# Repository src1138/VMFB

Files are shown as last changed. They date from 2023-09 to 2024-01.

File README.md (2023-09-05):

A vending machine for birds that rewards them with food when they drop something in a hole. Electronics and enclosure materials cost <100 USD/EUR. I've designed a PCB and PVC pipe enclosure and dispenser (described below). The circuit is not complex, but I think a custom PCB makes it easier for people who are not electronics hobbyists to build this. I've made a few different enclosures ouot of scrap for this, but will share the PVC pipe enclosure details since it's sturdy, waterproof, and the materials can all be found at the hardware store.

There were two main inspirations for me to start and  document this project

- Hans Forsberg (https://www.youtube.com/channel/UCtkv3wuEP-Veur4iYJWkBgA) - designed his own machine and was the first person I learned of that had birds (magpies) bringing items to deposit on thier own
- Josh Klein (https://thecrowbox.com/) - makes his Crowbox designs freely available and supports people who want to build it

# MAIN FEATURES
- portable
- saves power until a warm body is present
- battery or mains powered
- one moving part
- accessible components and materials
- rodents can't break in and get the food
- cheap to build
- customizable

# ELECTRONICS, SENSORS, AND POWER

The circuit is all analog, using four NE555 timers and one LM358 dual op amp. The sensors are all made using IR phototransistors and IR LEDs. The PCB has headers broken out so you can monitor and control it with a microcontroller or SBC. It runs on 5-6VDC and uses ~10mA in standby (~20mA if timer and powerbank keep-alive are enabled), ~250mA when IR LEDs are on and ~400mA when the dispenser motor is running. A 10,000 mAh USB powerbank should last about a week.

- Powerbank Keep-Alive: 555 sinks current every 7-22 seconds for 0.7-2.2 seconds to keep USB power banks on while sensors are in standby - the powerbank keep-alive can be disabled.
- IR LED ON/OFF: 555 keeps the IR LEDs used by the sensors on for 22 seconds after the last PIR trigger
- Op Amps: LM358 used as comparators to adjust the threshold of the sensors and send signals when they are triggered
- Motor Controller: 555 turns on the dispenser vibration motor when the deposit sensors are triggered, tuns it off when the dispense sensor is triggered
- Timed Dispense: 555 dispenses food every 10-100min - timed dispense can be disabled
- Daytimer: Phototransistor that puts the timer in reset while it's dark outside - brightness threshold can be adjusted or disabled (Rev. B)
- PIR Sensor: Sends a signal to turn on the sensor IR LEDs
- Deposit/Dispense Sensors: IR phototransistors and IR LEDs used as proximity sensors to monitor the deposit and dispense chutes
- Hopper Level Sensor: IR phototransistor and IR LED to detect when the food level gets low (Rev. B)
- Monitoring/Control: lines for monitoring and triggering events with an external controller (Rev. B)

# PCB, BOM AND GERBERS

Kicad Files (Github): https://github.com/src1138/VMFB

Gerbers and PCB (PCBWay): https://www.pcbway.com/project/shareproject/Vending_Machine_for_Birds_eda585b3.html

Front


Back


The PCB has footprints for USB type A, USB type B, barrel jack and screw terminal power input. You only need to populate the ones you will use.

In Rev.B Ver.1.0 you need to add a 10K resistor on the EMPTY sensor from the SIGNAL header pin to ground.

The Timer and Powerbank Keep-Alive are not essential and you don't have to populate the parts for them if you don't need/want to use them.

# CRITICAL COMPONENTS

This project uses commodity components, and you can confidently use alternatives with similar specs. There are a few points to keep in mind.

- For the phototransistors, they should have a photocurrent of around 10mA. If they have a lower photocurrent, you should replace the 10K resistors on the non-invertine op amp imputs with a higher value. For  instance, if your phototransistors have a photocurrent of ~1mA, use a 100K resistor intead.
- I use NE555Ps here - you could use other models, but keep in mind that the transistors controlling the IR LEDs (BD139) and motor (TIP41C) need a bit of current to their base. If for instance you use the CMOS 555 that can only source about 10mA, you may need to replace these transistors with ones that have more gain.

# HOW IT WORKS

## States
- Standby - No PIR trigger in the last 22 secs (IR LEDs are off)
- Sensors On - PIR was triggered in the last 22 secs (IR LEDs are on)
- Dispensing - Dispenser motor is on

## Modes

- Normal (dispenses on deposit)
- Timer (dispenses every x minutes AND dispenses on deposit)

## Event Sequence

1. PIR sensor sees a warm body
2. PIR triggers IR LED 555
3. IR LED 555 turn on sensor IR LEDs for 22 secs after last PIR trigger
4. When something is dropped in the deposit hole, the deposit sensor sees it
5. The deposit side of the dual op amp sends a pulse to trigger the motor 555
6. The motor 555 turns on the vibration dispenser motor - it times out after 11 secs
7. When something is dispensed, the dispense sensor sees it 
8. The dispense side of the dual op amp sends a pulse to reset the motor 555
9. The dispenser motor is stopped

When timed dispense is triggered, it sends a signal to turn on the sensor IR LEDs and triggers the motor controller to start the vibration dispenser. When something is dispensed, the motor stops.

# FAILURE MODES
- Deposit sensor jammed: Sensor will not trigger a dispense event until it is unjammed. The sensor uses an inline capacitor to limit the signal to a pulse each time it is triggered.
- Dispense sensor jammed: Vending machine will not dispense until the sensor is unjammed.
- Peanut hopper jammed or empty: Dispense motor will stop after ~10 seconds.

# MONITORING

I was using a Rasperry Pi Zero W with a wide-angle camera module with my vending machine, but I wanted something that drew less power (and was cheaper and more available). I found that the ESP32-CAM module  consumes about 135 MA when streaming video, can be put to sleep (consuming just a few mA) and has 4 GPIO pins available when using the SD-card slot - it can stream/record video and log events from the vending machine, making it all available over wifi or bluetooth.

I'm still in the process of modifying the ESP32-CAM example program to monitor/log events and stream video, record video files to SD, and sleep until the PIR is triggered. I will put this code on Github when it's ready.

# DISPENSER, ENCLOSURE, AND MOUNTING

Dispenser: two-layer vibration platform with offset holes made from 3mm PVC sheet and 15mm M3 brass standoffs. I used a small 24x12mm 2VDC motor attached to the dispenser with brass standoffs and 3mm PVC sheet.


Enclosure: made from 110mm and 50mm PVC pipe and joints, 32mm PVC joints, a 35mm plastic tray and a 1.5l PET bottle. 


Mounting: can be mounted on the ground, horizontal or vertical railing, wooden fence, wall, pole 
The dispenser typically dispenses a peanut or two within 3 seconds. Since it is a vibration dispenser, the enclosure should be level and mounted securely to insure relaible dispensing. 

The dispenser drops peanuts into a funnel made from the top of the PET bottle. There is about 12cm between the two, making it difficult for rodents small enough to get into the machine to get to the food. PVC is tough enough to keep larger rodents from gnawing or breaking thier way in.

# FEED

I used peanuts in the shell to attract birds to the area and shelled peanuts in the vending machine. If you live in an area with lots of pigeons, using peanuts in the shell will not attract them as much since they can't eat them (can't get he shell off) and you have a better chance of attracting corvids. Shelled peanuts are easier to dispense reliably - peanuts in the shell are less dense, more irregular in shape, and jam easily. Dry cat and dog food also works.

# BIRD CONDITIONING

Along with learning and having some fun, the goal is to get a birds to bring something, drop it in a hole, and get a reward. Birds need some conditioning for this, so there are a few phases to progress though to help them figure this out.

## Conditioning Stages
0 - Put food in the area you plan to mount the vending machine to start attracting birds
(1-2 weeks)
1 - Food Provided, Timed Dispense, Deposit Provided
(2-3 weeks)
2 - No Food Provided, Timed Dispense, Deposit Provided
(3-4 months)
3 - No Food Provided, No Timed Dispense, Deposit Provided
(6-8 months)
4 - No Food Provided, No Timed Dispense, No Deposit Provided

Time estimates are based on my own experience over the past year or so, but Phase 3 duration is a guess. As of July 2023 I have not yet seen a bird deposit an item I didn't provide. Unfortunately I had to take my machine down in May due to some new HOA regulations prohibiting feeding the birds in my neighborhood. I plan to redeploy it when I find another suitable location.

# PVC ENCLOSURE 

The PVC enclosure contains the battery, electronics and sensors, dispenser, peanuts, and deposited items. The platform is a 35cm plastic tray for a plant pot, attached to the deposit chute with 4 90-degree brackets, four M4 bolts and two hose clamps.

I used bits of electrical or duct tape to make the PVC pipes and joints fit securely tight. This way it is easy to disassemble/modify/repair. It's a good idea to wrap upward-facing joints to prevent water ingress during heavy rains.

You can load peanuts (or whatever) by unscrewing the top cap and pouring them in. I made two baffles from 3mm PVC sheet to reduce the pressure on the vibration dispenser.

You can unload the deposited items by unscrewing one of the caps on the lower half of the vending machine.

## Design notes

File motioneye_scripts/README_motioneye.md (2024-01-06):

GPIO Pins Used
You can use whatever pins you want, but I chose the following as they all default as inputs at boot.
- Sensor IR Control (SIRCON)=25 
- Dispenser Control (DISCON)=11
- PIR Monitor=27
- Sensor IR Monitor=17
- Timer Monitor=22
- Feed Level Monitor=23
- Deposit Monitor=24 
- Dispense Monitor=10 

/boot/config.txt
Add the following to make your control outputs drive low
gpio=11,25=op,dl

All the scripts go in /data/etc/
- userinit.sh: turns off HDMI and starts logging and camera enable/disable scripts
- VMFB_logger.py: logs the deposit and dispense events
- VMFB_logger.sh: logs PIR, Sensor IR, Timer and Feed Level status and trigger counts
- camera_on-off_schedule: sets the time for the camera to be enabled and disabled to save power
- monitor_1: displays logging and monitoring information on the video overlay
- alarm_on_1 and alarm_off_1: show as action buttons on the web interface to manually start and stop recording
- down_1: show as action buttons on the web interface to manually dispense feed

Config files also go in /data/etc/
- camera-1.conf (camera-1.conf.enable_camera/camera-1.conf.disable_camera): configuration files are overwritten to enable/disable the camera before restarting the motioneye server
- motion.conf (motion.conf.enable_camera/motion.conf.disable_camera): configuration files are overwritten to enable/disable the camera before restarting the motioneye server

Logs will be generated in /data/log/
- VMFB_YYY-MM-DD.log: daily log of events
- userinit.log: logs output from scripts called from userinit.sh
- prev_valPIR, prev_valSIR, prev_valTMR, prev_valEMT: logs the state of the previous execution of the VMFB_logger.sh so only changes will be logged
- 

If you want to specify timed dispense in a script instead of using the 555-based timer, you can try out VMFB_timer.sh.

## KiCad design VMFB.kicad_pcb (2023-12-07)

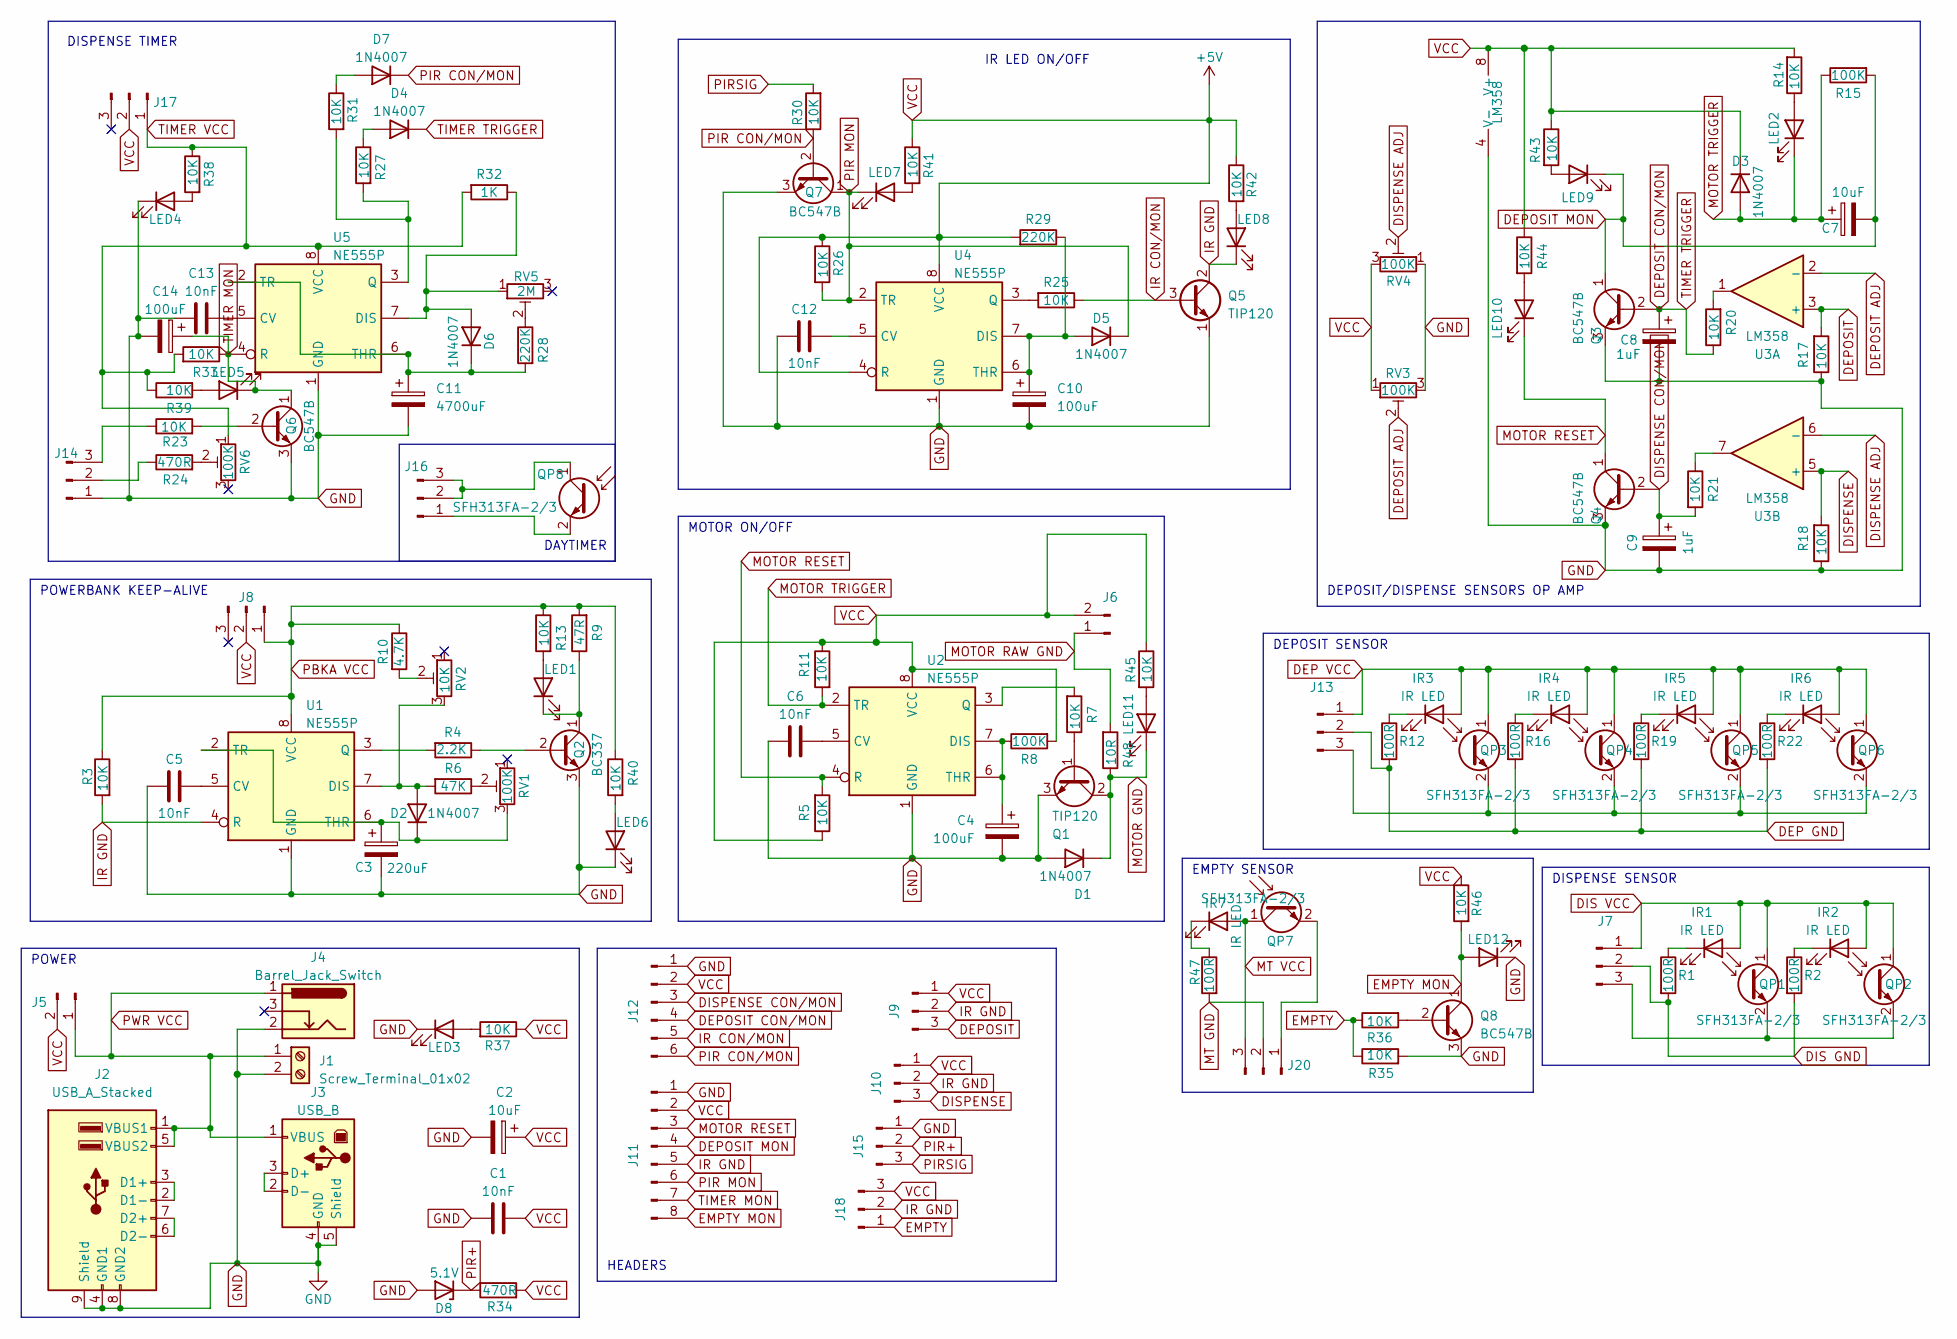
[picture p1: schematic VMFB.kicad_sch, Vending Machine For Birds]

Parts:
C1, C5, C6, C12, C13: 10nF; C_Disc_D5.0mm_W2.5mm_P5.00mm
C2, C7: 10uF; CP_Radial_D5.0mm_P2.00mm
C3: 220uF; CP_Radial_D8.0mm_P3.50mm
C4, C10, C14: 100uF; CP_Radial_D6.3mm_P2.50mm
C8, C9: 1uF; CP_Radial_D5.0mm_P2.00mm
C11: 4700uF; CP_Radial_D16.0mm_P7.50mm
D1, D2, D3, D4, D5, D6, D7: 1N4007; D_DO-41_SOD81_P2.54mm_Vertical_KathodeUp
D8: 5.1V; D_DO-41_SOD81_P2.54mm_Vertical_KathodeUp
IR1, IR2, IR3, IR4, IR5, IR6, IR7: IR LED; LED_D5.0mm
J1: Screw_Terminal_01x02; TerminalBlock_Altech_AK300-2_P5.00mm
J2: USB_A_Stacked; USB_A_Wuerth_61400826021_Horizontal_Stacked
J3: USB_B; USB_B_Lumberg_2411_02_Horizontal
J4: Barrel_Jack_Switch; BarrelJack_Horizontal
J5, J6: Conn_01x02_Pin; PinHeader_1x02_P2.54mm_Vertical
J7, J8, J9, J10, J13, J14, J15, J16, J17, J18, J20: Conn_01x03_Pin; PinHeader_1x03_P2.54mm_Vertical
J11: Conn_01x08_Pin; PinHeader_1x08_P2.54mm_Vertical
J12: Conn_01x06_Pin; PinHeader_1x06_P2.54mm_Vertical
LED1, LED2, LED3, LED4, LED5, LED6, LED7, LED8, LED9, LED10, LED11, LED12: Signal LED; LED_D5.0mm
Q1, Q5: TIP120; TO-220-3_Vertical
Q2: BC337; TO-92_Inline_Wide
Q3, Q4, Q6, Q7, Q8: BC547B; TO-92_Inline_Wide
QP1, QP2, QP3, QP4, QP5, QP6, QP7, QP8: SFH313FA-2/3; LED_D5.0mm
R1, R2, R12, R16, R19, R22, R47: 100R; R_Axial_DIN0207_L6.3mm_D2.5mm_P2.54mm_Vertical
R3, R5, R7, R11, R13, R14, R17, R18, R20, R21, R23, R25, R26, R27, R30, R31, R33, R35, R36, R37, R38, R39, R40, R41, R42, R43, R44, R45, R46: 10K; R_Axial_DIN0207_L6.3mm_D2.5mm_P2.54mm_Vertical
R4: 2.2K; R_Axial_DIN0207_L6.3mm_D2.5mm_P2.54mm_Vertical
R6: 47K; R_Axial_DIN0207_L6.3mm_D2.5mm_P2.54mm_Vertical
R8, R15: 100K; R_Axial_DIN0207_L6.3mm_D2.5mm_P2.54mm_Vertical
R9: 47R; R_Axial_DIN0309_L9.0mm_D3.2mm_P2.54mm_Vertical
R10: 4.7K; R_Axial_DIN0207_L6.3mm_D2.5mm_P2.54mm_Vertical
R24, R34: 470R; R_Axial_DIN0207_L6.3mm_D2.5mm_P2.54mm_Vertical
R28, R29: 220K; R_Axial_DIN0207_L6.3mm_D2.5mm_P2.54mm_Vertical
R32: 1K; R_Axial_DIN0207_L6.3mm_D2.5mm_P2.54mm_Vertical
R48: 10R; R_Axial_DIN0414_L11.9mm_D4.5mm_P5.08mm_Vertical
RV1, RV3, RV4, RV6: 100K; Potentiometer_Piher_PT-10-V10_Vertical
RV2: 10K; Potentiometer_Piher_PT-10-V10_Vertical
RV5: 2M; Potentiometer_Piher_PT-10-V10_Vertical
U1, U2, U4, U5: NE555P; DIP-8_W7.62mm
U3: LM358; DIP-8_W7.62mm

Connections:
DEP GND: J13.2, R12.2, R16.2, R19.2, R22.2
DEP VCC: IR3.2 (A), IR4.2 (A), IR5.2 (A), IR6.2 (A), J13.1, QP3.1 (C), QP4.1 (C), QP5.1 (C), QP6.1 (C)
DEPOSIT: J9.3, R17.2, U3.3 (+)
DEPOSIT ADJ: RV3.2, U3.2 (-)
DEPOSIT CON/MON: C8.1, D4.1 (K), J12.4, Q3.2 (B), R20.1
DEPOSIT MON: C7.2, J11.4, LED9.1 (K), Q3.1 (C), R15.2
DIS GND: J7.2, R1.2, R2.2
DIS VCC: IR1.2 (A), IR2.2 (A), J7.1, QP1.1 (C), QP2.1 (C)
DISPENSE: J10.3, R18.2, U3.5 (+)
DISPENSE ADJ: RV4.2, U3.6 (-)
DISPENSE CON/MON: C9.1, J12.3, Q4.2 (B), R21.2
EMPTY: J18.1, R35.1, R36.1
EMPTY MON: J11.8, LED12.2 (A), Q8.1 (C), R46.2
GND: C1.2, C2.2, C3.2, C4.2, C5.2, C6.2, C8.2, C9.2, C10.2, C11.2, C12.2, C13.2, C14.2, D1.2 (A), D8.2 (A), J1.2, J2.4 (GND1), J2.8 (GND2), J2.9 (Shield), J3.4 (GND), J3.5 (Shield), J4.2, J11.1, J12.1, J14.1, J15.1, LED3.1 (K), LED4.1 (K), LED6.1 (K), LED12.1 (K), Q1.3 (E), Q2.3 (E), Q3.3 (E), Q4.3 (E), Q5.1 (E), Q6.3 (E), Q7.3 (E), Q8.3 (E), R17.1, R18.1, R35.2, RV3.3, RV4.1, U1.1 (GND), U2.1 (GND), U3.4 (V-), U4.1 (GND), U5.1 (GND)
IR CON/MON: J12.5, Q5.3 (B), R25.1
IR GND: J9.2, J10.2, J11.5, J18.2, LED8.1 (K), Q5.2 (C), R3.2, U1.4 (R)
MOTOR GND: D1.1 (K), LED11.1 (K), Q1.2 (C), R48.1
MOTOR RAW GND: J6.1, R48.2
MOTOR RESET: J11.3, LED10.1 (K), Q4.1 (C), R5.2, U2.4 (R)
MOTOR TRIGGER: C7.1, D3.2 (A), LED2.1 (K), R11.2, R15.1, U2.2 (TR)
MT GND: J20.2, R47.2
MT VCC: IR7.2 (A), J20.3, QP7.1 (C)
unnamed: D2.2 (A), R6.2, RV2.3, U1.7 (DIS)
unnamed: C3.1, D2.1 (K), RV1.3, U1.2 (TR), U1.6 (THR)
unnamed: D4.2 (A), R27.1
unnamed: C10.1, D5.2 (A), R29.1, U4.6 (THR), U4.7 (DIS)
unnamed: D6.2 (A), R32.1, RV5.1, U5.7 (DIS)
unnamed: C11.1, D6.1 (K), R28.2, U5.2 (TR), U5.6 (THR)
unnamed: D7.2 (A), R31.1
unnamed: IR1.1 (K), R1.1
unnamed: IR2.1 (K), R2.1
unnamed: IR3.1 (K), R12.1
unnamed: IR4.1 (K), R16.1
unnamed: IR5.1 (K), R19.1
unnamed: IR6.1 (K), R22.1
unnamed: IR7.1 (K), R47.1
unnamed: J2.2 (D1-), J2.3 (D1+)
unnamed: J2.6 (D2-), J2.7 (D2+)
unnamed: J3.2 (D-), J3.3 (D+)
unnamed: J7.3, QP1.2 (E), QP2.2 (E)
unnamed: J13.3, QP3.2 (E), QP4.2 (E), QP5.2 (E), QP6.2 (E)
unnamed: J14.2, R24.1
unnamed: J14.3, R23.1
unnamed: J16.1, QP8.2 (E)
unnamed: J16.2, J16.3, QP8.1 (C)
unnamed: J20.1, QP7.2 (E)
unnamed: LED1.2 (A), R13.2
unnamed: LED1.1 (K), Q2.1 (C), R9.1
unnamed: LED2.2 (A), R14.1
unnamed: LED3.2 (A), R37.2
unnamed: LED4.2 (A), R38.2
unnamed: LED5.2 (A), R39.2
unnamed: LED6.2 (A), R40.2
unnamed: LED7.2 (A), R41.2
unnamed: LED8.2 (A), R42.2
unnamed: LED9.2 (A), R43.2
unnamed: LED10.2 (A), R44.2
unnamed: LED11.2 (A), R45.2
unnamed: Q1.1 (B), R7.1
unnamed: Q2.2 (B), R4.1
unnamed: Q6.2 (B), R23.2
unnamed: Q8.2 (B), R36.2
unnamed: R6.1, RV1.2
unnamed: R10.2, RV2.2
unnamed: R20.2, U3.1
unnamed: R21.1, U3.7
unnamed: R24.2, RV6.2
unnamed: R28.1, RV5.2
unnamed: C5.1, U1.5 (CV)
unnamed: R4.2, U1.3 (Q)
unnamed: C6.1, U2.5 (CV)
unnamed: C4.1, R8.1, U2.6 (THR), U2.7 (DIS)
unnamed: R7.2, U2.3 (Q)
unnamed: C12.1, U4.5 (CV)
unnamed: R25.2, U4.3 (Q)
unnamed: C13.1, U5.5 (CV)
unnamed: R27.2, R31.2, U5.3 (Q)
PBKA VCC: J8.1, R3.1, R9.2, R10.1, R13.1, R40.1, U1.8 (VCC)
PIR CON/MON: D7.1 (K), J12.6, Q7.2 (B), R30.1
PIR MON: D5.1 (K), J11.6, LED7.1 (K), Q7.1 (C), R26.2, U4.2 (TR)
PIR+: D8.1 (K), J15.2, R34.1
PIRSIG: J15.3, R30.2
PWR VCC: J1.1, J2.1 (VBUS1), J2.5 (VBUS2), J3.1 (VBUS), J4.1, J5.1
TIMER MON: C14.1, J11.7, LED5.1 (K), Q6.1 (C), R33.1, U5.4 (R)
TIMER VCC: J17.1, R32.2, R33.2, R38.1, R39.1, RV6.1, U5.8 (VCC)
VCC: C1.1, C2.1, D3.1 (K), J5.2, J6.2, J8.2, J9.1, J10.1, J11.2, J12.2, J17.2, J18.3, R5.1, R8.2, R11.1, R14.2, R26.1, R29.2, R34.2, R37.1, R41.1, R42.1, R43.1, R44.1, R45.1, R46.1, RV3.1, RV4.3, U2.8 (VCC), U3.8 (V+), U4.4 (R), U4.8 (VCC)

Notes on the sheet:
DISPENSE SENSOR
POWER
DEPOSIT SENSOR
MOTOR ON/OFF
EMPTY SENSOR
DISPENSE TIMER
HEADERS
POWERBANK KEEP-ALIVE
IR LED ON/OFF
DAYTIMER
DEPOSIT/DISPENSE SENSORS OP AMP

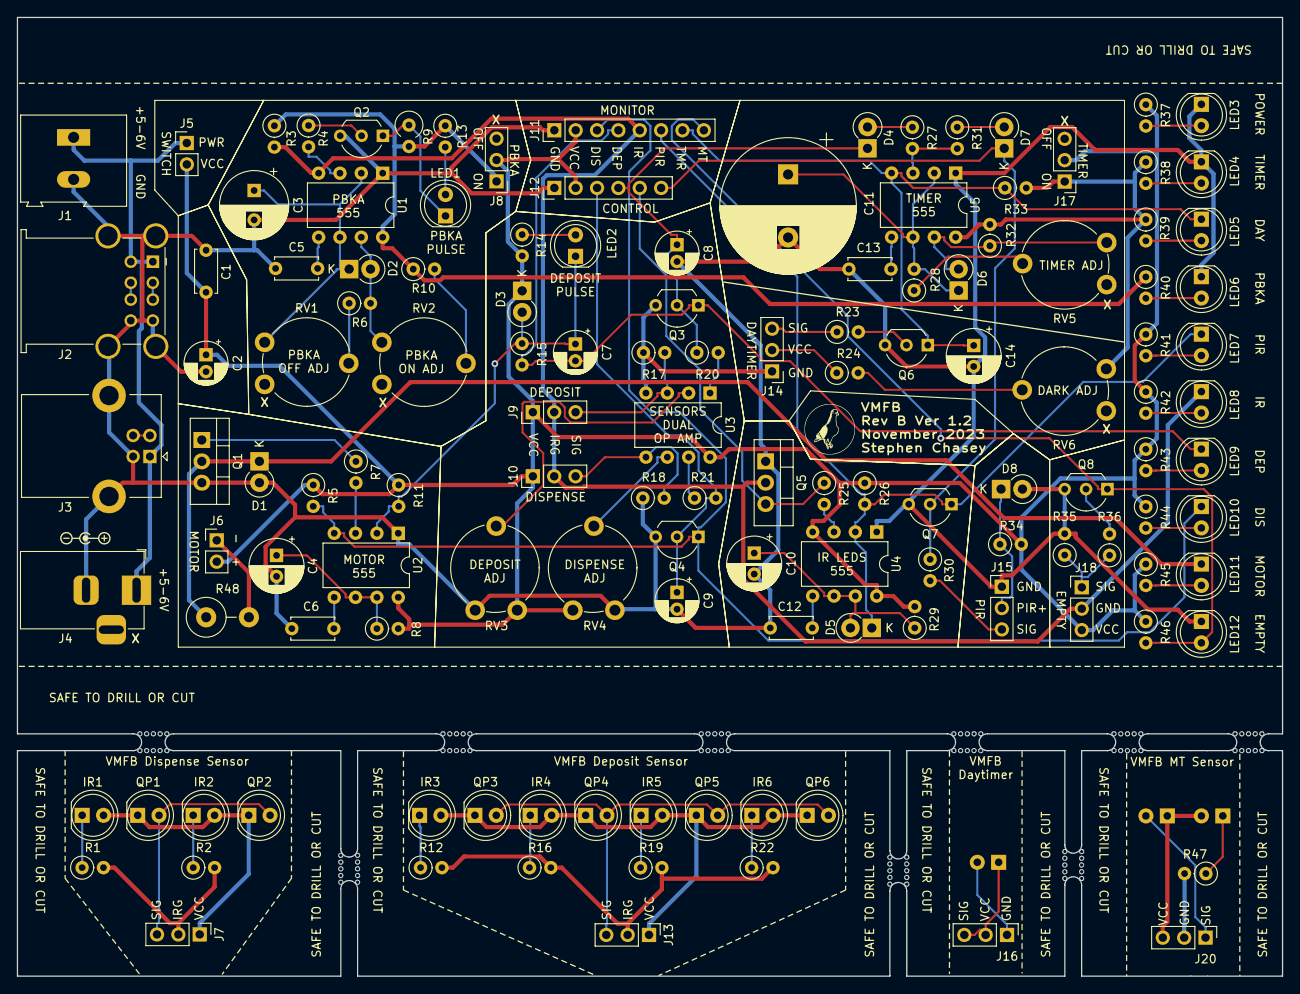
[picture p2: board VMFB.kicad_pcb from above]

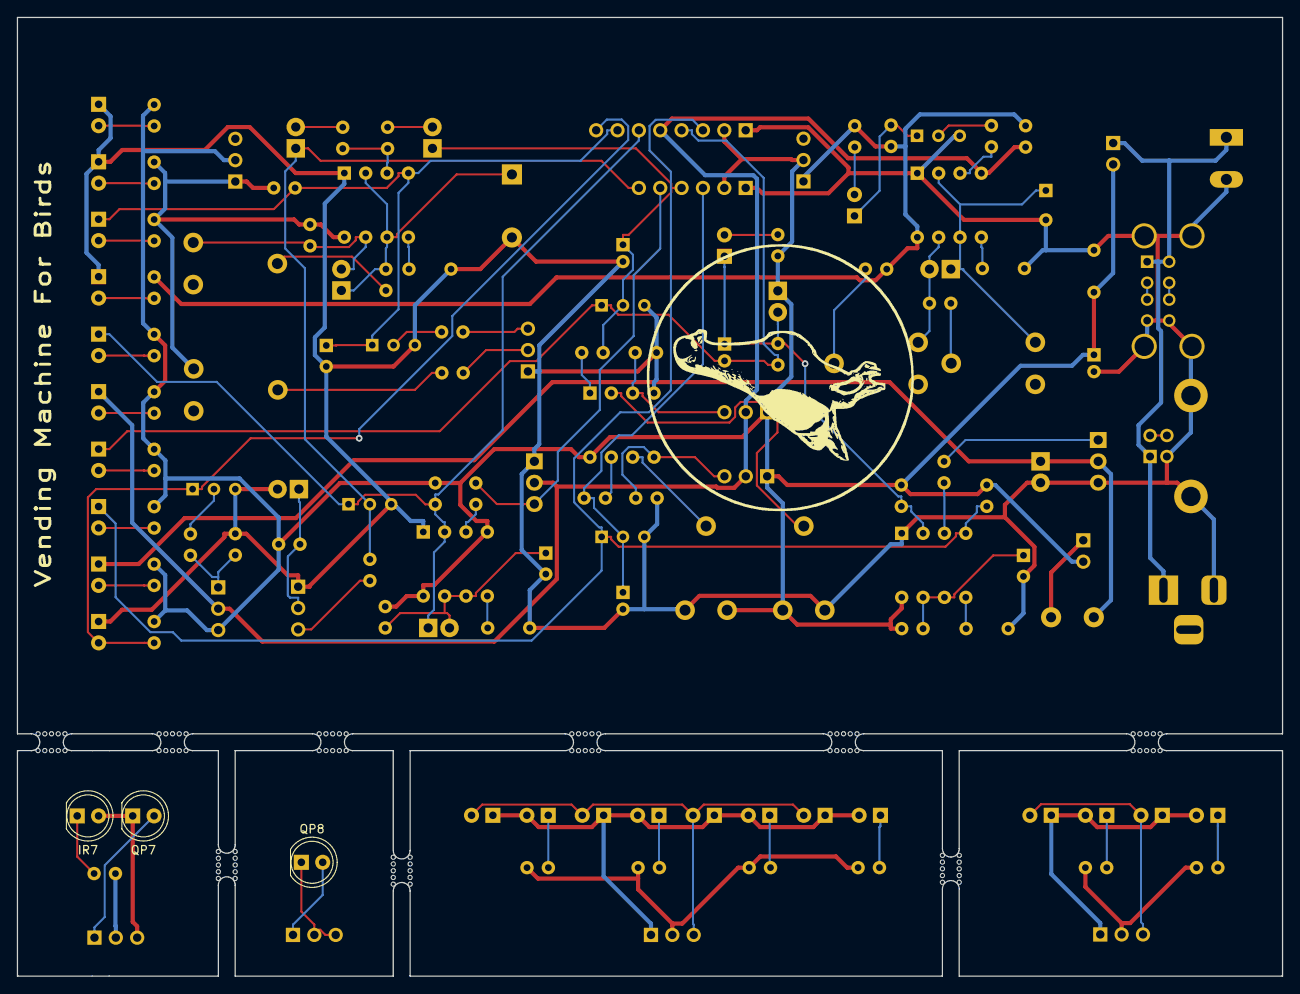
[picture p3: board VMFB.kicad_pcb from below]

Board: 2 copper layers, 150.4 x 114.0 mm, 138 parts (4 on the bottom side), 86 nets.

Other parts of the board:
DIRTY BIRD: LOGO
Polarity: Center Pos; LOGO
Small Dirty Bird: LOGO

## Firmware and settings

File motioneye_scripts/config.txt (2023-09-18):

gpu_mem=128
gpu_mem_256=128
gpu_mem_512=128
dtparam=i2c_arm=on
dtparam=i2s=on
dtparam=spi=on
dtparam=audio=on
disable_camera_led=1
arm_freq=950
gpu_freq=250
sdram_freq=450
over_voltage=0
# Set pins 11 (DIS) and 25 (PIR) to be outputs driving low to avoid them
# staying high on statup
gpio=11,25=op,dl
# Set pins 10, 17, 22, 23, 24, 27 to be inputs with pull-ups
# gpio=10,17,22,23,24,27=ip,pu

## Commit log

2023-05-09 Adding VMFB Kicad project/schematic/pcb files
    [VMFB.kicad_pcb, VMFB.kicad_sch]
2023-05-09 Update README.md
    Adding general info about the circuit.
2023-05-17 Added 1uf cap on the dispense transistor base to prevent triggering on power-up.
    [VMFB.kicad_pcb, VMFB.kicad_sch]
2023-05-22 Swapped PIR+ and GND to better accomodate common PIR pinouts.
    [VMFB.kicad_pcb, VMFB.kicad_sch]
2023-05-23 Added 100K bleeder resistor across the pulse-shortening cap C7
    [VMFB.kicad_pcb, VMFB.kicad_sch]
2023-05-23 changed external header to 6-pin with pinout to match most 4-channel level shifters, removed 2 unnecessary 10K reset resistors from timer and IR power 555s
    [VMFB.kicad_pcb, VMFB.kicad_sch]
2023-05-23 added another 1uf cap across the dispense sensor so like the dispense sensor it won't trigger on power up.
    [VMFB.kicad_pcb, VMFB.kicad_sch]
2023-05-23 added resistor and diode to turn IR LEDs on when the timer triggers so the dispense sensors can stop the motor
    [VMFB.kicad_pcb, VMFB.kicad_sch]
2023-05-23 a few small tweaks, connecting the switch pin of the barrel jack to ground
    [VMFB.kicad_pcb, VMFB.kicad_sch]
2023-05-23 tweaked silkscreen labels
    [VMFB.kicad_pcb]
2023-05-29 changed signal LED resistors to 10K from 1K.
    [VMFB.kicad_pcb, VMFB.kicad_sch]
2023-06-02 Update README.md
    Added link to PCBWay shared project for gerbers and BOM.
2023-06-02 Update README.md
    Adding some images of the board.
2023-06-04 added monitoring-only header, moved IR LED switch transistor from VCC to GND and removed a pin from the sensor headers (no need for separate VCC for the IR LEDS), 100R to 47R on Q$ base, 47R to 22R o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
    [VMFB.kicad_pcb, VMFB.kicad_sch]
2023-06-05 moved dispense monitoring directly to the collector of Q2 so you can tell if it's jammed
    [VMFB.kicad_pcb, VMFB.kicad_sch]
2023-06-05 updated version to 1.3
    [VMFB.kicad_pcb, VMFB.kicad_sch]
2023-06-05 updated control header label and changed footprint for BC547 two commits ago
    [VMFB.kicad_pcb]
2023-06-08 added LDR-based light sensor to turn off timed dispense when the sun sets
    [VMFB.kicad_pcb, VMFB.kicad_sch]
2023-06-12 improvements to the daytimer, and added an LED so you can see the status
    [VMFB.kicad_pcb, VMFB.kicad_sch]
2023-06-12 minor adjustments to the daytimer
    [VMFB.kicad_pcb, VMFB.kicad_sch]
2023-06-13 more adjustments to the daytimer
    [VMFB.kicad_pcb, VMFB.kicad_sch]
2023-06-14 more adjustments to the daytimer and cleaned up schematic a bit
    [VMFB.kicad_pcb, VMFB.kicad_sch]
2023-06-16 added box labels to schematic, bit more tweaking on the PCB
    [VMFB.kicad_pcb, VMFB.kicad_sch]
2023-06-20 schematic rearranging, swapped LDR for phototransistor on the Daytimer, added peanut hopper empty sensor, pcb rearranging
    [VMFB.kicad_pcb, VMFB.kicad_sch]
2023-06-20 tweakedcomponent placement on Daytimer
    [VMFB.kicad_pcb]
2023-06-21 marked different modules on the PCB, reannotated, small placement adjustments
    [VMFB.kicad_pcb, VMFB.kicad_sch]
2023-06-23 schematic cleanup, pcb tweaking
    [VMFB.kicad_pcb, VMFB.kicad_sch]
2023-06-25 schemati and pcb tweaking
    [VMFB.kicad_pcb, VMFB.kicad_sch]
2023-06-26 schematic and pcb tweaking
    [VMFB.kicad_pcb, VMFB.kicad_sch]
2023-06-27 removed 10K resistor to ground fromo empty sensor
    [VMFB.kicad_pcb, VMFB.kicad_sch]
2023-06-27 removed transistor/resistor disabline PBKA when IR is on = grounding this along with the IR and signal LEDs instead of using another transistor
    [VMFB.kicad_pcb, VMFB.kicad_sch]
2023-06-28 small tweaks and corrected 'Deposit Pulse' LED label (was 'Dispense Pulse')
    [VMFB.kicad_pcb]
2023-07-03 added transistor to the PBKA
    [VMFB.kicad_pcb, VMFB.kicad_sch]
2023-07-03 added logo
    [VMFB.kicad_pcb]
2023-07-04 fixed timer connection to trigger IR LEDs
    [VMFB.kicad_pcb, VMFB.kicad_sch]
2023-07-04 more cleanup
    [VMFB.kicad_pcb]
2023-07-10 Added space for 1.6mm tab routing
    Added space for tab routing so PCBway doesn't have to modify the board before fabrication. Makes ordering easier, slightly cheaper and looks nicer.
    [VMFB.kicad_pcb]
2023-07-10 Delete ~VMFB.kicad_sch.lck
    removing lock file
2023-07-11 more pcb tweaks
    [VMFB.kicad_pcb]
2023-07-12 changing route paths from 1.6mm to 2.0mm - PCBWay says min of 1.6, but boards I have received have 2.0mm wide panel routes
    [VMFB.kicad_pcb]
2023-07-17 added 2mm tab routes with break holes to the pcb based on what PCBWay has done to panelize previous versions
    [VMFB.kicad_pcb]
2023-07-27 Fixed some component names.
    [VMFB.kicad_pcb, VMFB.kicad_sch]
2023-08-02 fixed dark sensor - connected BC547B emitter to IR GND net (was connected to ground, so base was always triggering the transistor a little due to IR GND being .7 volts above actual ground)
    [VMFB.kicad_pcb, VMFB.kicad_sch]
2023-08-02 fixed dark sensor - added 10K resistor grounding the phototransistor output
    [VMFB.kicad_pcb, VMFB.kicad_sch]
2023-08-03 changed 1K resistor on empty sensor to 100R
    [VMFB.kicad_sch]
2023-08-04 PCB tweaking
    Changed R7 footprint to 11.5x4.5. Marked off Dark Sensor and moved logo and version. Flipped R11.
    [VMFB.kicad_pcb, VMFB.kicad_sch]
2023-08-06 Added routing
    [VMFB.kicad_pcb]
2023-08-14 removed unnecessary 470R from Daytimer module
    [VMFB.kicad_pcb, VMFB.kicad_sch]
2023-08-14 adding routes
    [VMFB.kicad_pcb]
2023-08-15 changed 470R to 1K on the Daytimer
    [VMFB.kicad_pcb, VMFB.kicad_sch]
2023-08-19 updated routing - no vias
    [VMFB.kicad_pcb]
2023-08-23 tweaked routing
    [VMFB.kicad_pcb]
2023-08-24 Update README.md
    Updated PCB images to latest version RevB V1.1.
2023-09-05 adding monitor file for motioneyeos to display status (PIR/Sensors/Timer/Feed Hopper) - the file needs to be executable and goes in /data/etc/
2023-09-06 adding motioneyeos action button scripts to manually turn the sensors on or dispense a peanut by clicking a button
2023-09-07 working ok - if you use pins 12 and 13 for the manual sensor activation and dispensing, you should add this to your config.txt: gpio=12,16=op,dl
2023-09-07 added deposit and dispense sensor jam detection
2023-09-12 moved logging to python for interrupt support, turning off hdmi in userinit.sh
2023-09-13 record video while the sensors are on
2023-09-13 buttons to disable/enable the camera
2023-09-14 adding example camera and motion config files
2023-09-14 adding script to schedule camera enable/disable
2023-09-14 adding camera enable/disable scheduler
2023-09-14 debugging camera scheduler
2023-09-18 more debugging, added timer script
    [config.txt]
2023-09-18 debugging camera on/off scheduler
2023-11-21 replaced TIP41 and BC137 with TIP120s, changed empty sensor from beam break to proximity
    [VMFB.kicad_pcb, VMFB.kicad_sch]
2023-12-07 updating netclasses, adding routing
    [VMFB.kicad_pcb, VMFB.kicad_sch]
2023-12-07 cleaned up tracks
    [VMFB.kicad_pcb]
